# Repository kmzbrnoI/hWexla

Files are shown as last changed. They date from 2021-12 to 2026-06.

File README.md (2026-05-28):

hWexla – Switch motor
=====================

hWexla is a switch motor designed in [Model Railroader Club Brno I](https://kmz-brno.cz/)
to switch their turnouts. The project is opensource & openhardware, this repository
contains all data.

## Features

* Model 9g servo used as a drive force.
* Magnetic detection of movement. No mechanical parts detecting servo movement.
* Installation via unified D-SUB 25 connector.
* 2 inputs for position setting.
* 2 outputs for position indication (up to 200 mA).
* 2 IO pins for debug/panel.
* 2×3 relay for switching track current (up to 3 A).
* Diagnostic interface.
* IO protection.
* Slave mode.
* Input voltage: 10–20 V.
* Stabilizing of servo-voltage is solved in external board – hWexla contains
  only connector. Stepdowns like [RB0005](https://github.com/RoboticsBrno/RB0005-UniversalStepDown)
  are expected to be used.

## Parts

1. [PCB](pcb)
2. [Firmware](fw)
3. [WEXLACON PCB](wexlacon)
4. [Diagnostic PCB](diagpcb)

## [Requirements](requirements.md)

In czech only

## Piece check

Pass following checks to mark a piece of (newly manufactured) hWexla as
*quality check pass*.

1. Optical inspection.
2. Check programming interface is working.
3. Check diagnostic interface is working (browser visible, accepting commands).
4. Check all inputs are working (browser + functional test).
5. Check all outputs are working (browser + HW tester).
6. Check servo moves in full range.
7. Check magnet values, test signalization of end-position-reached.
8. Check relay output.
9. Monitor recorded minimum&maximum servo voltage.
10. Check for errors/warnings (browser).

## Authors

hWexla was designed in [Model Railroaders Club
Brno](https://www.kmz-brno.cz/) by [Jan Horáček](mailto:jan.horacek@kmz-brno.cz).

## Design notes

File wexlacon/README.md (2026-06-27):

WEXLACON
========

WEXLACON is a PCB permanently mounted to the railway layout to which hWexla connects.

Schematic and the PCB was designed in KiCad 9.

## Authors

hWexla was designed in [Model Railroaders Club
Brno](https://www.kmz-brno.cz/) by [Jan Horáček](mailto:jan.horacek@kmz-brno.cz).

## License

Content of this directory is provided under [Creative Commons
Attribution-ShareAlike 4.0
License](https://creativecommons.org/licenses/by-sa/4.0/) as openhardware
project. You may download any data, contribute to the project, manufacture PCB
yourself or even sell it yourself.

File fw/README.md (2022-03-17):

# hWexla firmware

## Build & requirements

This firmware is developed in C language, compiled via `avr-gcc` with help
of `make`. You may also find tools like `avrdude` helpful.

Hex files are available in *Releases* section.

## Programming

Firmware could be programmed directly to board via ISP programming connector.

Flash main application & fuses:

```bash
$ make
$ make fuses
$ make program
```

## Author's toolkit

Text editor + `make`. No more, no less.

## License

This application is released under the [Apache License v2.0
](https://www.apache.org/licenses/LICENSE-2.0).

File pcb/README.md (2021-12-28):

hWexla PCB
==========

See main repository readme for more information.

## License

Content of this directory is provided under [Creative Commons
Attribution-ShareAlike 4.0
License](https://creativecommons.org/licenses/by-sa/4.0/) as openhardware
project. You may download any data, contribute to the project, create PCB
yourself or even sell it yourself.

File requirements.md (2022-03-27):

Požadavky na přestavník hWexla
==============================

## Vstupy/výstupy

1. Přestavník má
 * 2 vstupy na nastavení polohy (z MTB),
 * 2 vstupy/výstupy do pultu/testovací krabičky,
 * 2 výstupy indikující polohu (do MTB).
2. Vstupy z MTB mají vždy přednost nad vstupy z přestavníku.
3. Všechny vstupy jsou chráněny proti přepětí.
4. Všechny výstupy jsou formou otevřeného kolektoru do maximálního externího
   napětí 30 V. Výstupy jsou chráněny proti přepětí.

## Hardware

1. Přestavník je chráněn proti přepětí. Připojení přepětí ho nepoškodí.
   Ochrana proti přepětí je samovratná.
2. Přestavník je chráněn proti opačné polaritě napájení. Připojení opačného
   napájení ho nepoškodí. Ochrana proti opačnému napájení je samovratná.
3. Přestavník je chráněn proti poruše serva. Při zkratu na servu dojde
   k přepálení nevratné pojistky.
4. Výstup stabilizovaných 5 V ven z desky je chráněn pojistkou.
5. Testovací a digitální vstupy a výstupy jsou chráněny proti krátkým napěťovým
   špičkám.
6. Stabilizace napájení pro servo je řešená pomocí externího modulu. Očekávaný
   je pulzní stepdown. Vyčlenění stabilizace z hlavní DPS umožňuje její snadné
   nahrazení například v případě nedostupných součástek.
7. Garantovaný proud přes relé je 3 A.

## Software

1. Relé se připíná uprostřed chodu přestavníku.
2. V případě nefunkčnosti serva (např. odpojení), je při manuálním dojetí
   do polohy správně ovládáno relé.
3. Koncová poloha je indikována na základě hodnot z magnetického senzoru.
   Hodnoty ze senzoru jinak nemají na funkci přestavníku žádný další vliv.
4. Přestavník kontroluje napájení serva.
5. Přestavník indikuje svůj stav pomocí LED.
6. Z přestavníku je možné číst diagnostická data pomocí USART rozhraní.
7. Pomocí testovací krabičky je možné nastavit obě koncové polohy.
8. Při startu přestavník zapne napájení serva až po pseudo-náhodné době, aby
   se rozložila proudová zátěž při zapínání kolejiště s mnoha přestavníky.

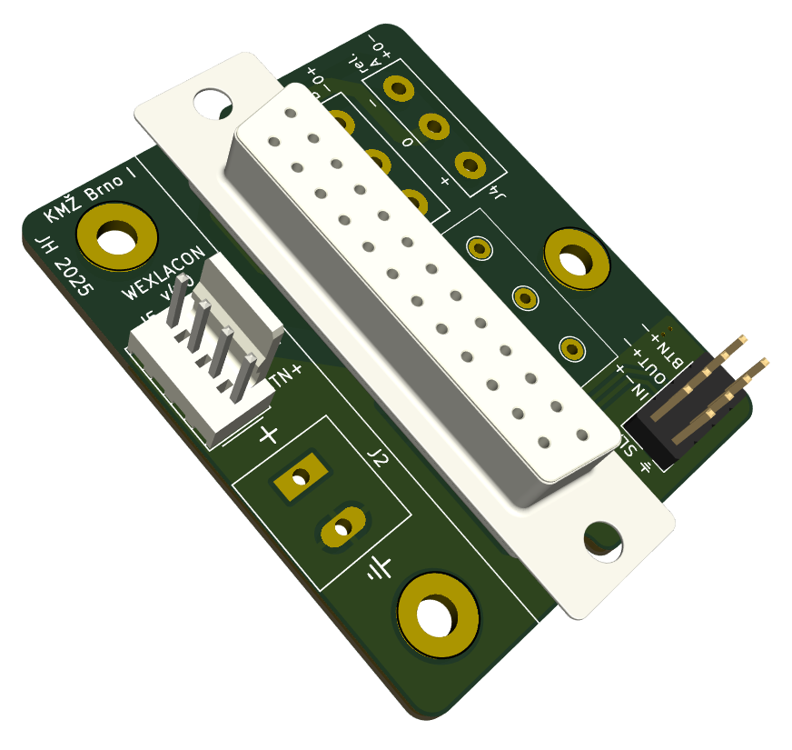
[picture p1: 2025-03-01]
wexlacon/export/wexlacon-3d.png

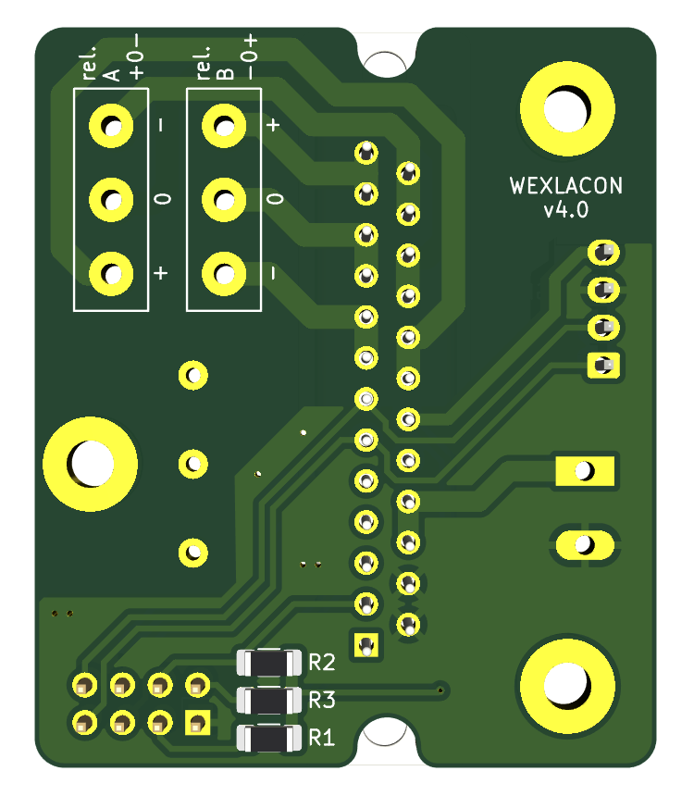
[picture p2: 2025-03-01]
wexlacon/export/wexlacon-bot.png

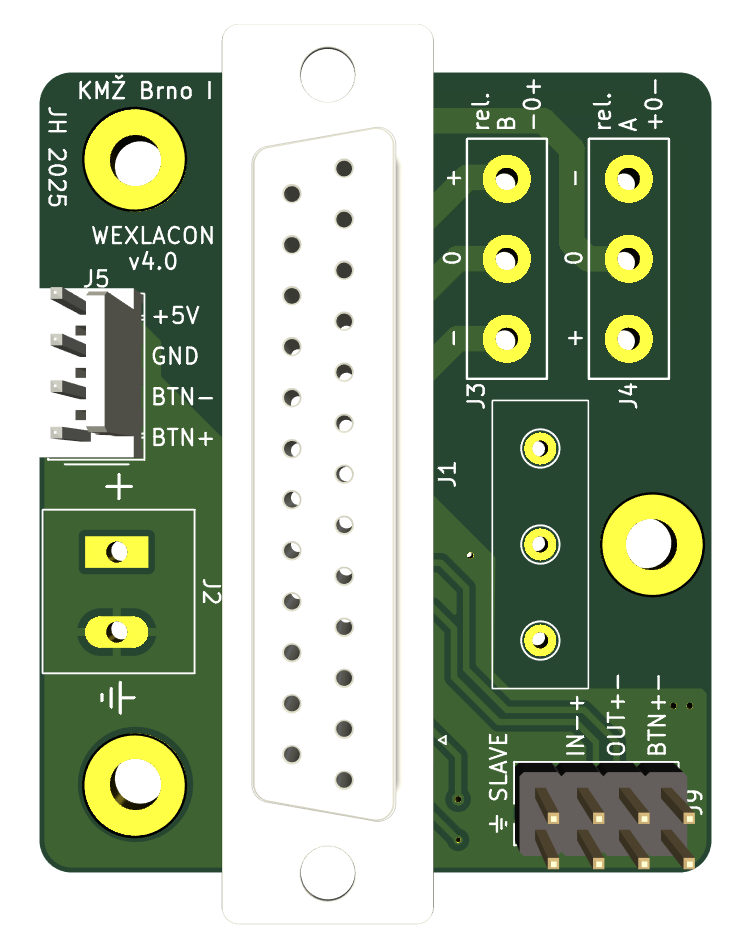
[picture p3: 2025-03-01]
wexlacon/export/wexlacon-top.png

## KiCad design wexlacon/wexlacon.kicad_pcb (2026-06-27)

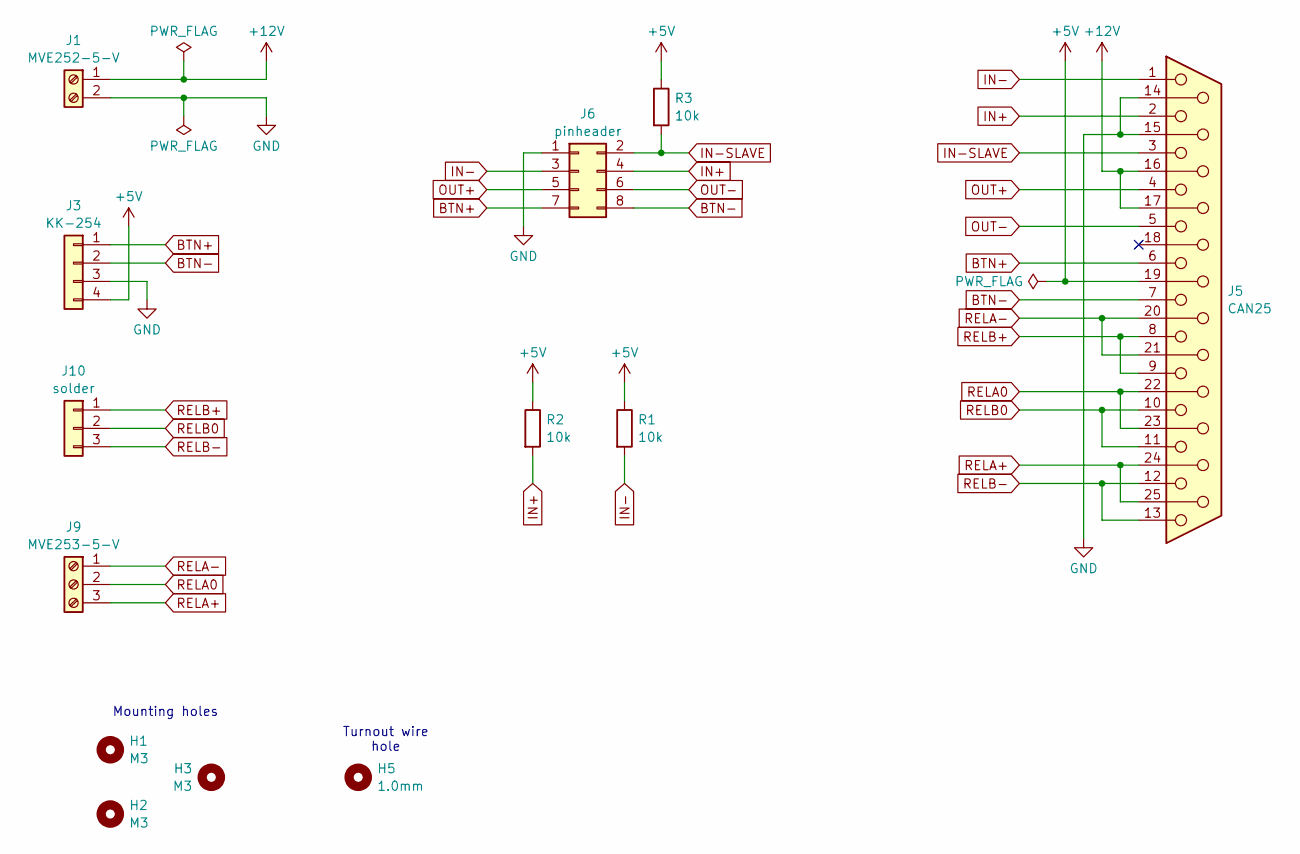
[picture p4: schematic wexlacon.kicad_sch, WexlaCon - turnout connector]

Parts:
H1, H2, H3: M3; MountingHole_3.2mm_M3_Pad
H5: 1.0mm; TestPoint_THTPad_D2.0mm_Drill1.0mm
J1: MVE252-5-V
J3: KK-254; Molex_KK-254_AE-6410-04A_1x04_P2.54mm_Vertical
J5: CAN25; DSUB-25_Female_Vertical_P2.77x2.84mm
J6: pinheader; PinHeader_2x04_P2.54mm_Vertical
J9: MVE253-5-V; RELAYCON
J10: solder; RELAYCON
R1, R2, R3: 10k; R_1206_3216Metric_Pad1.30x1.75mm_HandSolder

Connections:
+5V: J3.4, J5.19, R1.1, R2.1, R3.1
+12V: J1.1, J5.16, J5.17
BTN+: J3.1, J5.6, J6.7
BTN-: J3.2, J5.7, J6.8
GND: J1.2, J3.3, J5.14, J5.15, J6.1
IN+: J5.2, J6.4, R2.2
IN-: J5.1, J6.3, R1.2
IN-SLAVE: J5.3, J6.2, R3.2
OUT+: J5.4, J6.5
OUT-: J5.5, J6.6
RELA0: J5.22, J5.23, J9.2
RELA+: J5.24, J5.25, J9.3
RELA-: J5.20, J5.21, J9.1
RELB0: J5.10, J5.11, J10.2
RELB+: J5.8, J5.9, J10.1
RELB-: J5.12, J5.13, J10.3

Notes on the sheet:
Mounting holes
Turnout wire hole

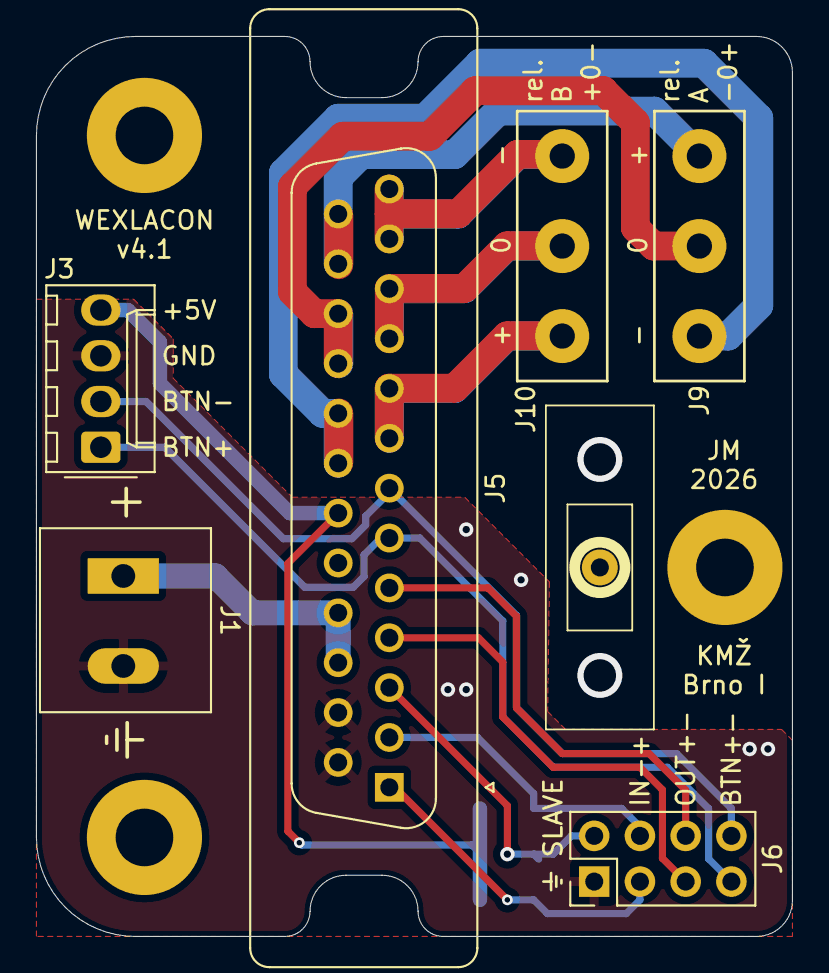
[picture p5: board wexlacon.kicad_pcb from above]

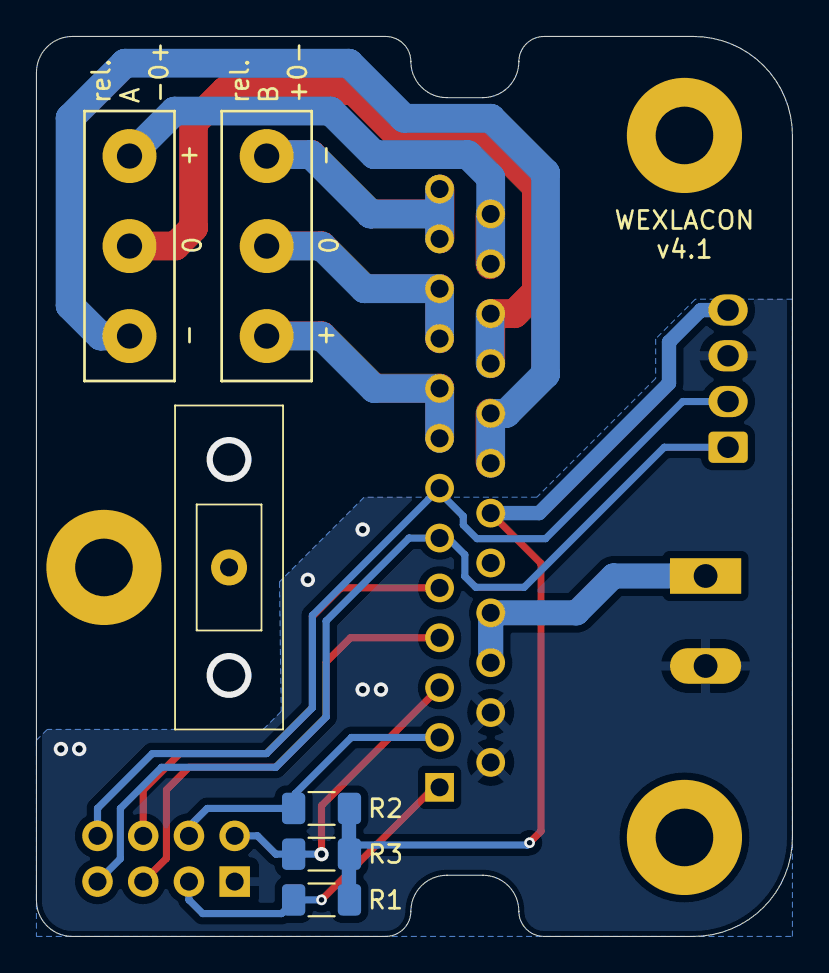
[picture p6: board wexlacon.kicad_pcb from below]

Board: 2 copper layers, 42.0 x 50.0 mm, 13 parts (3 on the bottom side), 16 nets.

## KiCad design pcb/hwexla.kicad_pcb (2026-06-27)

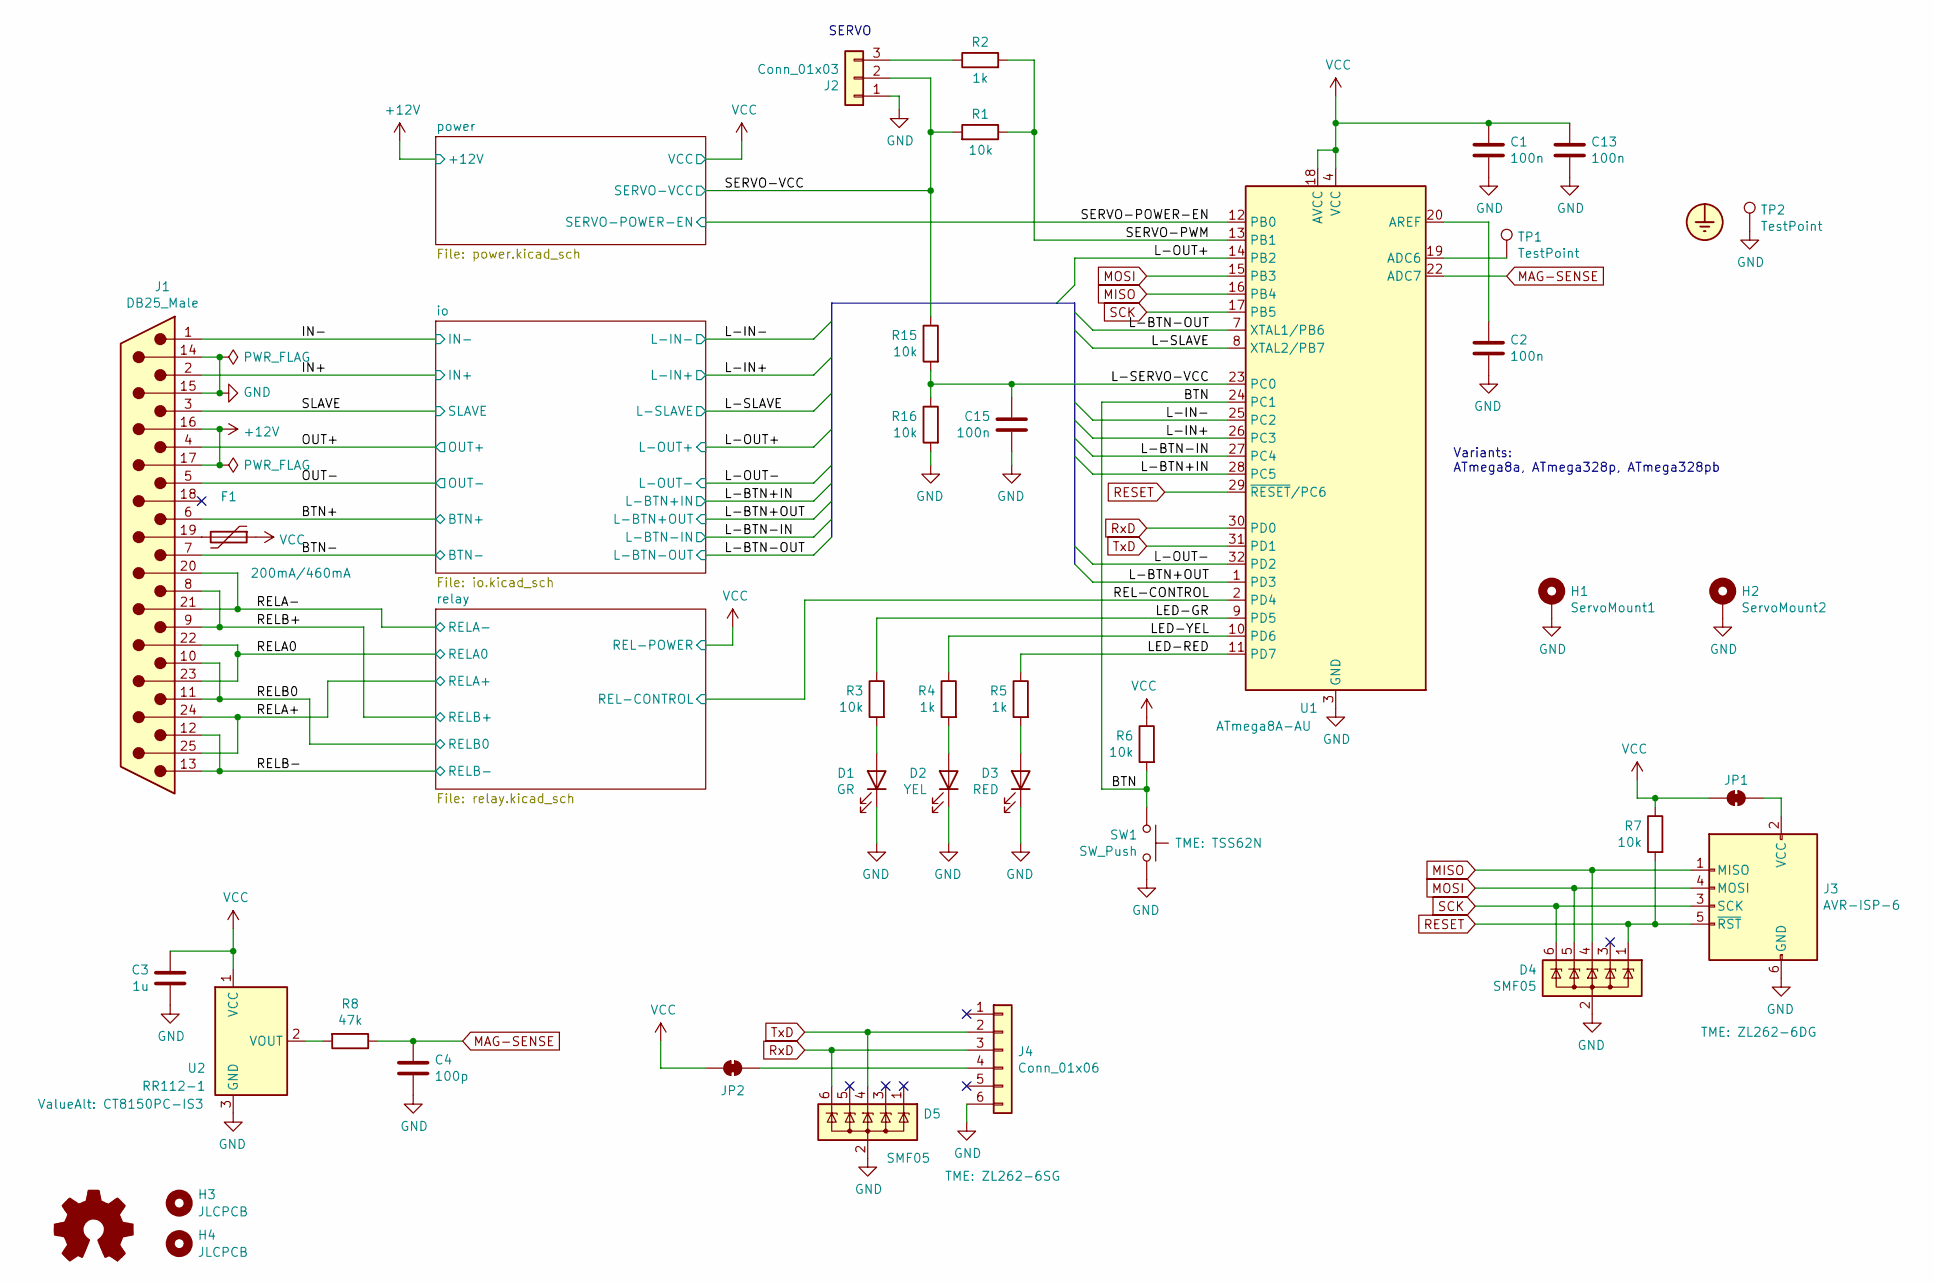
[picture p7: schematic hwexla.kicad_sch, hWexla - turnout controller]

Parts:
C1, C2, C13, C15: 100n; C_0805_2012Metric_Pad1.18x1.45mm_HandSolder; LCSC C49678
C3: 1u; C_0805_2012Metric_Pad1.18x1.45mm_HandSolder; LCSC C28323
C4: 100p; C_0805_2012Metric_Pad1.18x1.45mm_HandSolder; LCSC C1790
D1: GR; LED_0805_2012Metric_Pad1.15x1.40mm_HandSolder; LCSC C2297
D2: YEL; LED_0805_2012Metric_Pad1.15x1.40mm_HandSolder; LCSC C2296
D3: RED; LED_0805_2012Metric_Pad1.15x1.40mm_HandSolder; LCSC C84256
D4, D5: SMF05; SOT-363_SC-70-6; LCSC C15879
F1: 200mA/460mA; Fuse_1206_3216Metric_Pad1.42x1.75mm_HandSolder; LCSC C69680
H1: ServoMount1; MountingHole_2.2mm_M2_Pad
H2: ServoMount2; MountingHole_2.2mm_M2_Pad
H3, H4: JLCPCB; ToolingHole_1.152mm; JLCPCB_IGNORE true
J1: DB25_Male; DSUB-25_Male_EdgeMount_P2.77mm; JLCPCB_IGNORE true
J2: Conn_01x03; PinHeader_1x03_P2.54mm_Vertical; JLCPCB_IGNORE true
J3: AVR-ISP-6; PinSocket_2x03_P2.54mm_Vertical; JLCPCB_IGNORE true
J4: Conn_01x06; PinSocket_1x06_P2.54mm_Vertical; JLCPCB_IGNORE true
JP1, JP2: SolderJumper-2_P1.3mm_Bridged_RoundedPad1.0x1.5mm
R1, R3, R6, R7, R15, R16: 10k; R_0805_2012Metric_Pad1.20x1.40mm_HandSolder; LCSC C17414
R2, R4, R5: 1k; R_0805_2012Metric_Pad1.20x1.40mm_HandSolder; LCSC C17513
R8: 47k; R_0805_2012Metric_Pad1.20x1.40mm_HandSolder; LCSC C17713
SW1: SW_Push; SW_SPST_Omron_B3FS-100xP; JLCPCB_IGNORE true
TP1: TestPoint; TestPoint_Pad_D1.5mm
TP2: TestPoint; TestPoint_Loop_D1.80mm_Drill1.0mm_Beaded; JLCPCB_IGNORE true
U1: ATmega8A-AU; TQFP-32_7x7mm_P0.8mm; LCSC C16190
U2: RR112-1; SOT-23W; JLCPCB_IGNORE true

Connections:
+12V: J1.16, J1.17; also elsewhere on the board
/BTN: R6.2, SW1.2, U1.24 (PC1)
/BTN+: J1.6; also elsewhere on the board
/BTN-: J1.7; also elsewhere on the board
/IN+: J1.2; also elsewhere on the board
/IN-: J1.1; also elsewhere on the board
/L-BTN+IN: U1.28 (PC5); also elsewhere on the board
/L-BTN+OUT: U1.1 (PD3); also elsewhere on the board
/L-BTN-IN: U1.27 (PC4); also elsewhere on the board
/L-BTN-OUT: U1.7 (XTAL1/PB6); also elsewhere on the board
/L-IN+: U1.26 (PC3); also elsewhere on the board
/L-IN-: U1.25 (PC2); also elsewhere on the board
/L-OUT+: U1.14 (PB2); also elsewhere on the board
/L-OUT-: U1.32 (PD2); also elsewhere on the board
/L-SERVO-VCC: C15.1, R15.2, R16.1, U1.23 (PC0)
/L-SLAVE: U1.8 (XTAL2/PB7); also elsewhere on the board
/LED-GR: R3.1, U1.9 (PD5)
/LED-RED: R5.1, U1.11 (PD7)
/LED-YEL: R4.1, U1.10 (PD6)
/OUT+: J1.4; also elsewhere on the board
/OUT-: J1.5; also elsewhere on the board
/REL-CONTROL: U1.2 (PD4); also elsewhere on the board
/RELA0: J1.22, J1.23; also elsewhere on the board
/RELA+: J1.24, J1.25; also elsewhere on the board
/RELA-: J1.20, J1.21; also elsewhere on the board
/RELB0: J1.10, J1.11; also elsewhere on the board
/RELB+: J1.8, J1.9; also elsewhere on the board
/RELB-: J1.12, J1.13; also elsewhere on the board
/SERVO-POWER-EN: U1.12 (PB0); also elsewhere on the board
/SERVO-PWM: R1.1, R2.2, U1.13 (PB1)
/SERVO-VCC: J2.2, R1.2, R15.1; also elsewhere on the board
/SLAVE: J1.3; also elsewhere on the board
GND: C1.1, C2.1, C3.1, C4.2, C13.1, C15.2, D1.1 (K), D2.1 (K), D3.1 (K), D4.2 (A), D5.2 (A), H1.1, H2.1, J1.14, J1.15, J2.1, J3.6 (GND), J4.6, R16.2, SW1.1, TP2.1, U1.3 (GND), U1.5 (GND), U1.21 (GND), U2.3 (GND); also elsewhere on the board
MAG-SENSE: C4.1, R8.1, U1.22 (ADC7)
MISO: D4.4 (K), J3.1 (MISO), U1.16 (PB4)
MOSI: D4.5 (K), J3.4 (MOSI), U1.15 (PB3)
unnamed: D1.2 (A), R3.2
unnamed: D2.2 (A), R4.2
unnamed: D3.2 (A), R5.2
unnamed: F1.2, J1.19
unnamed: J2.3, R2.1
unnamed: J3.2 (VCC), JP1.1 (A)
unnamed: J4.4, JP2.2 (B)
unnamed: TP1.1, U1.19 (ADC6)
unnamed: C2.2, U1.20 (AREF)
unnamed: R8.2, U2.2 (VOUT)
RESET: D4.1 (K), J3.5 (~RST), R7.2, U1.29 (~RESET/PC6)
RxD: D5.6 (K), J4.3, U1.30 (PD0)
SCK: D4.6 (K), J3.3 (SCK), U1.17 (PB5)
TxD: D5.4 (K), J4.2, U1.31 (PD1)
VCC: C1.2, C3.2, C13.2, F1.1, JP1.2 (B), JP2.1 (A), R6.1, R7.1, U1.4 (VCC), U1.6 (VCC), U1.18 (AVCC), U2.1 (VCC); also elsewhere on the board

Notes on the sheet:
Variants: ATmega8a, ATmega328p, ATmega328pb
SERVO

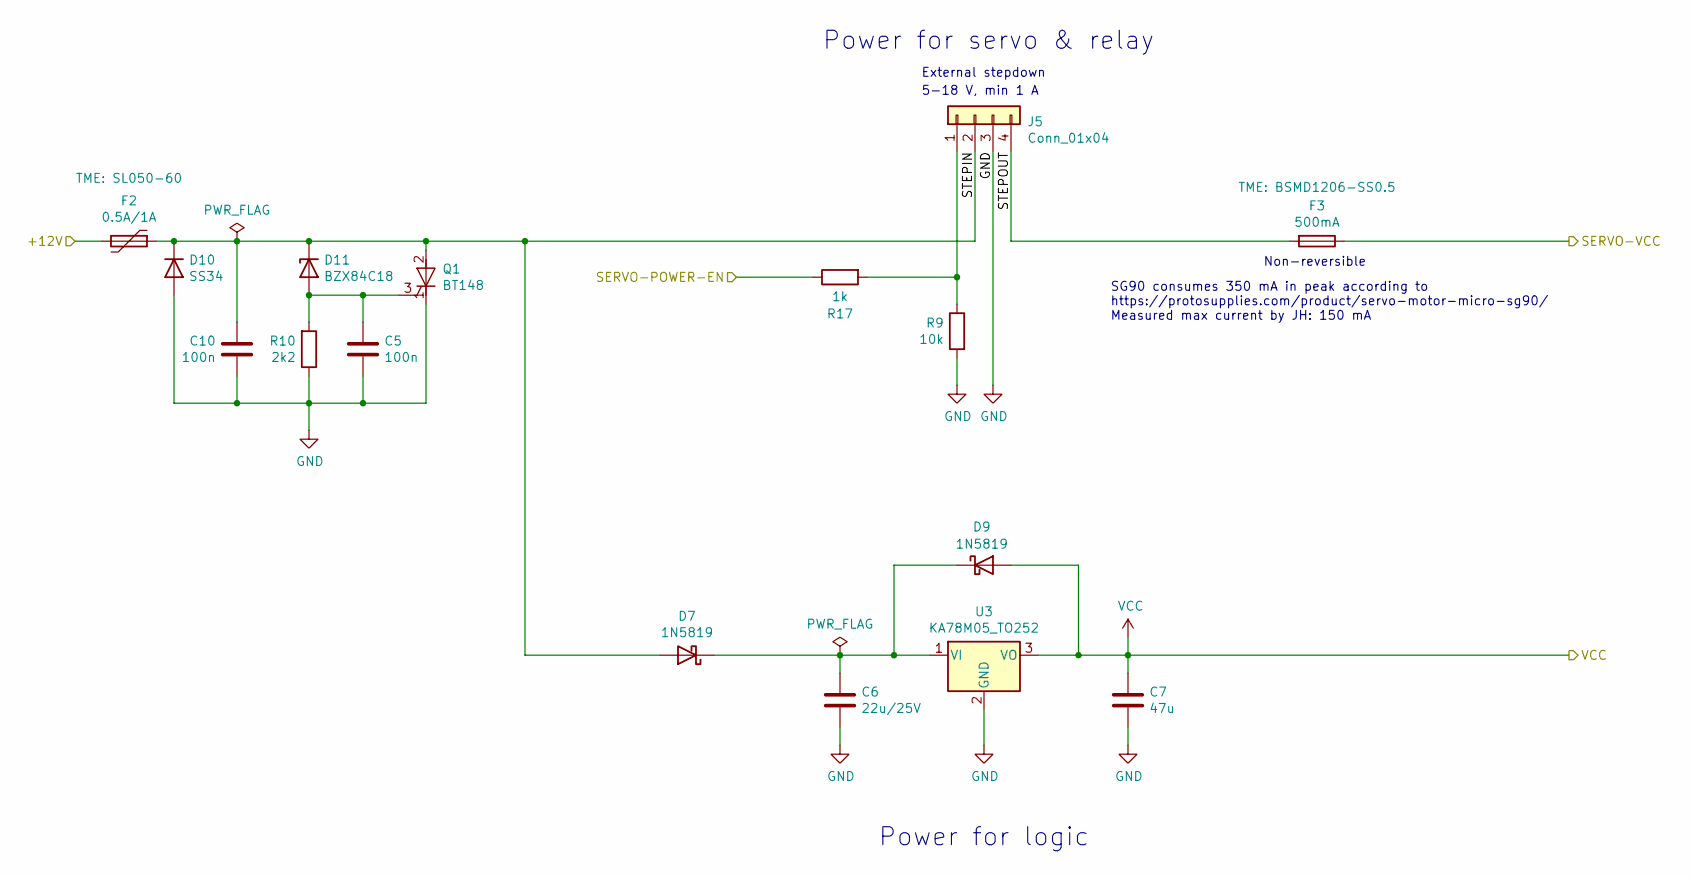
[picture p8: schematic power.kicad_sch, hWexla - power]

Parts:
C5, C10: 100n; C_0805_2012Metric_Pad1.18x1.45mm_HandSolder; LCSC C49678
C6: 22u/25V; C_0805_2012Metric; LCSC C45783
C7: 47u; C_0805_2012Metric; LCSC C16780
D7, D9: 1N5819; D_SOD-123; LCSC C191023
D10: SS34; D_SMA_Handsoldering; LCSC C8678
D11: BZX84C18; SOT-23; LCSC C841166
F2: 0.5A/1A; Fuse_2920_7451Metric; LCSC C2760297
F3: 500mA; Fuse_1206_3216Metric_Pad1.42x1.75mm_HandSolder; LCSC C3161978
J5: Conn_01x04; PinHeader_1x04_P2.54mm_Vertical; JLCPCB_IGNORE true
Q1: BT148; SOT-223; LCSC C256433
R9: 10k; R_0805_2012Metric_Pad1.20x1.40mm_HandSolder; LCSC C17414
R10: 2k2; R_0805_2012Metric_Pad1.20x1.40mm_HandSolder; LCSC C17520
R17: 1k; R_0805_2012Metric_Pad1.20x1.40mm_HandSolder; LCSC C17513
U3: KA78M05_TO252; TO-252-2; LCSC C58069

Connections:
+12V: F2.2; also elsewhere on the board
/SERVO-POWER-EN: R17.1; also elsewhere on the board
/SERVO-VCC: F3.1; also elsewhere on the board
/power/STEPIN: C10.1, D7.2 (A), D10.1 (K), D11.3 (K), F2.1, J5.2, Q1.2 (A)
/power/STEPOUT: F3.2, J5.4
GND: C5.2, C6.2, C7.2, C10.2, D10.2 (A), J5.3, Q1.1 (K), R9.2, R10.1, U3.2 (GND); also elsewhere on the board
unnamed: C6.1, D7.1 (K), D9.1 (K), U3.1 (VI)
unnamed: C5.1, D11.1 (A), Q1.3 (G), R10.2
unnamed: J5.1, R9.1, R17.2
VCC: C7.1, D9.2 (A), U3.3 (VO); also elsewhere on the board

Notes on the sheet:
Power for servo & relay
SG90 consumes 350 mA in peak according to https://protosupplies.com/product/servo-motor-micro-sg90/ Measured max current by JH: 150 mA
External stepdown
Non-reversible
Power for logic
5-18 V, min 1 A

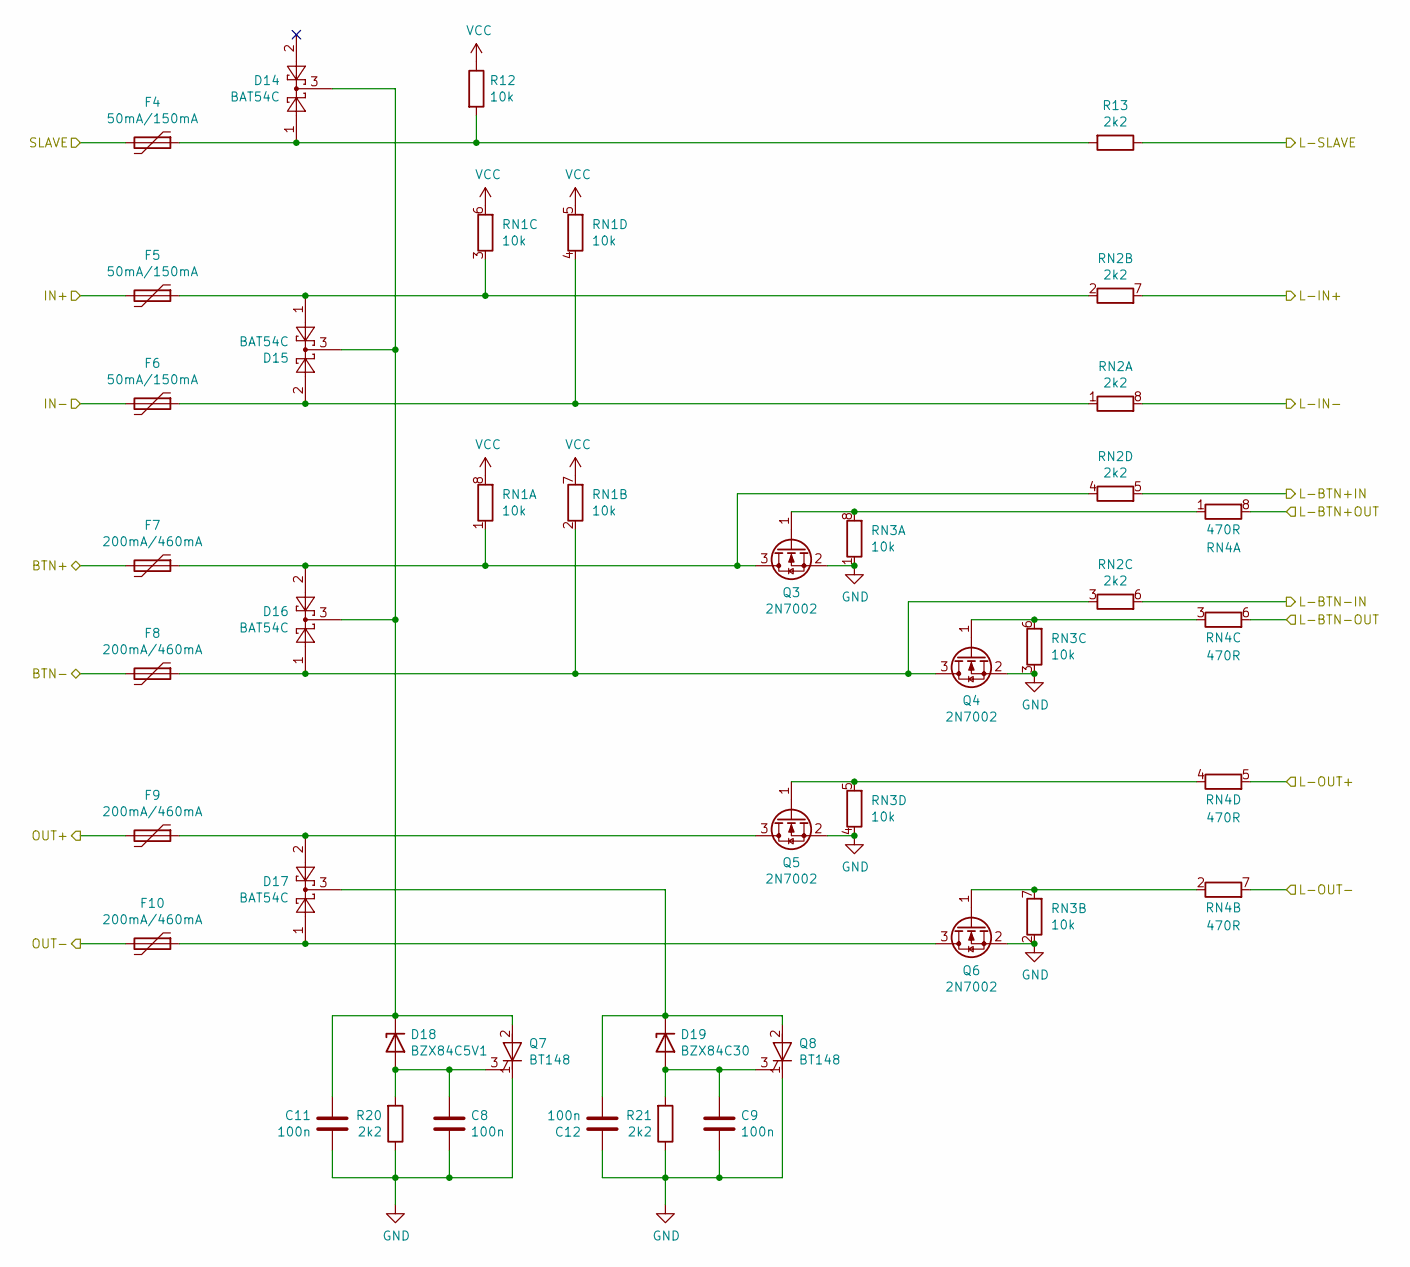
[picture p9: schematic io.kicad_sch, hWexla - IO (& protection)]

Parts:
C8, C9, C11, C12: 100n; C_0805_2012Metric_Pad1.18x1.45mm_HandSolder; LCSC C49678
D14, D15, D16, D17: BAT54C; SOT-23; LCSC C37704
D18: BZX84C5V1; SOT-23; LCSC C962733
D19: BZX84C30; SOT-23; LCSC C2926248
F4, F5, F6: 50mA/150mA; Fuse_1206_3216Metric_Pad1.42x1.75mm_HandSolder; LCSC C20797
F7, F8, F9, F10: 200mA/460mA; Fuse_1206_3216Metric_Pad1.42x1.75mm_HandSolder; LCSC C69680
Q3, Q4, Q5, Q6: 2N7002; SOT-23; LCSC C8545
Q7, Q8: BT148; SOT-223; LCSC C256433
R12: 10k; R_0805_2012Metric_Pad1.20x1.40mm_HandSolder; LCSC C17414
R13, R20, R21: 2k2; R_0805_2012Metric_Pad1.20x1.40mm_HandSolder; LCSC C17520
RN1, RN3: 10k; R_Array_Concave_4x0603; LCSC C396839
RN2: 2k2; R_Array_Concave_4x0603; LCSC C136829
RN4: 470R; R_Array_Concave_4x0603; LCSC C705088

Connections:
/BTN+: F7.2; also elsewhere on the board
/BTN-: F8.2; also elsewhere on the board
/IN+: F5.2; also elsewhere on the board
/IN-: F6.2; also elsewhere on the board
/L-BTN+IN: RN2.5 (R4.2); also elsewhere on the board
/L-BTN+OUT: RN4.8 (R1.2); also elsewhere on the board
/L-BTN-IN: RN2.6 (R3.2); also elsewhere on the board
/L-BTN-OUT: RN4.6 (R3.2); also elsewhere on the board
/L-IN+: RN2.7 (R2.2); also elsewhere on the board
/L-IN-: RN2.8 (R1.2); also elsewhere on the board
/L-OUT+: RN4.5 (R4.2); also elsewhere on the board
/L-OUT-: RN4.7 (R2.2); also elsewhere on the board
/L-SLAVE: R13.1; also elsewhere on the board
/OUT+: F9.2; also elsewhere on the board
/OUT-: F10.2; also elsewhere on the board
/SLAVE: F4.2; also elsewhere on the board
GND: C8.2, C9.2, C11.2, C12.1, Q3.2 (S), Q4.2 (S), Q5.2 (S), Q6.2 (S), Q7.1 (K), Q8.1 (K), R20.1, R21.1, RN3.1 (R1.1), RN3.2 (R2.1), RN3.3 (R3.1), RN3.4 (R4.1); also elsewhere on the board
unnamed: D14.1, F4.1, R12.2, R13.2
unnamed: C8.1, D18.1 (A), Q7.3 (G), R20.2
unnamed: C11.1, D14.3, D15.3, D16.3, D18.3 (K), Q7.2 (A)
unnamed: C9.1, D19.1 (A), Q8.3 (G), R21.2
unnamed: C12.2, D17.3, D19.3 (K), Q8.2 (A)
unnamed: D16.2, F7.1, Q3.3 (D), RN1.1 (R1.1), RN2.4 (R4.1)
unnamed: Q3.1 (G), RN3.8 (R1.2), RN4.1 (R1.1)
unnamed: D16.1, F8.1, Q4.3 (D), RN1.2 (R2.1), RN2.3 (R3.1)
unnamed: Q4.1 (G), RN3.6 (R3.2), RN4.3 (R3.1)
unnamed: D17.2, F9.1, Q5.3 (D)
unnamed: Q5.1 (G), RN3.5 (R4.2), RN4.4 (R4.1)
unnamed: D17.1, F10.1, Q6.3 (D)
unnamed: Q6.1 (G), RN3.7 (R2.2), RN4.2 (R2.1)
unnamed: D15.1, F5.1, RN1.3 (R3.1), RN2.2 (R2.1)
unnamed: D15.2, F6.1, RN1.4 (R4.1), RN2.1 (R1.1)
VCC: R12.1, RN1.5 (R4.2), RN1.6 (R3.2), RN1.7 (R2.2), RN1.8 (R1.2); also elsewhere on the board

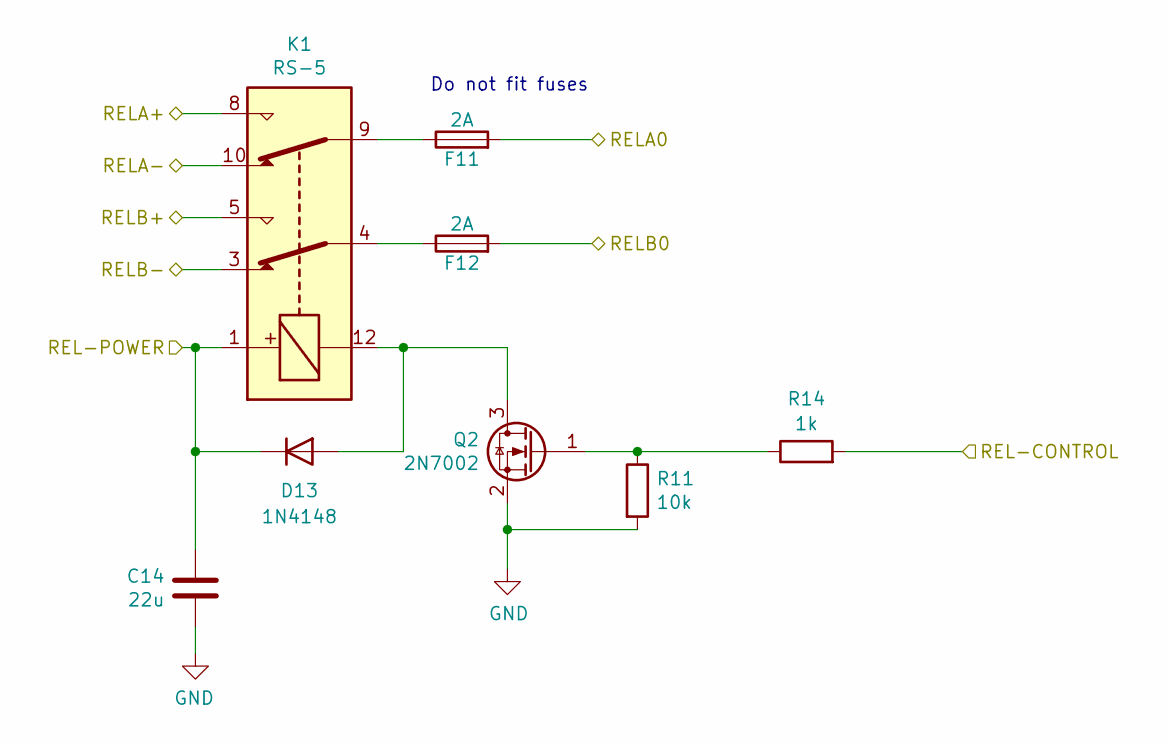
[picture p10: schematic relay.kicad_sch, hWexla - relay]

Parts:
C14: 22u; C_0805_2012Metric; LCSC C45783
D13: 1N4148; D_0805_2012Metric_Pad1.15x1.40mm_HandSolder; LCSC C2128
F11, F12: 2A; Fuse_1206_3216Metric_Pad1.42x1.75mm_HandSolder; LCSC C17888
K1: RS-5; HFD2; JLCPCB_IGNORE true
Q2: 2N7002; SOT-23; LCSC C8545
R11: 10k; R_0805_2012Metric_Pad1.20x1.40mm_HandSolder; LCSC C17414
R14: 1k; R_0805_2012Metric_Pad1.20x1.40mm_HandSolder; LCSC C17513

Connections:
/REL-CONTROL: R14.2; also elsewhere on the board
/RELA0: F11.2; also elsewhere on the board
/RELA+: K1.8; also elsewhere on the board
/RELA-: K1.10; also elsewhere on the board
/RELB0: F12.2; also elsewhere on the board
/RELB+: K1.5; also elsewhere on the board
/RELB-: K1.3; also elsewhere on the board
GND: C14.2, Q2.2 (S), R11.2; also elsewhere on the board
unnamed: D13.2 (A), K1.12, Q2.3 (D)
unnamed: F11.1, K1.9
unnamed: F12.1, K1.4
unnamed: Q2.1 (G), R11.1, R14.1
VCC: C14.1, D13.1 (K), K1.1; also elsewhere on the board

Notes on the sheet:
Do not fit fuses

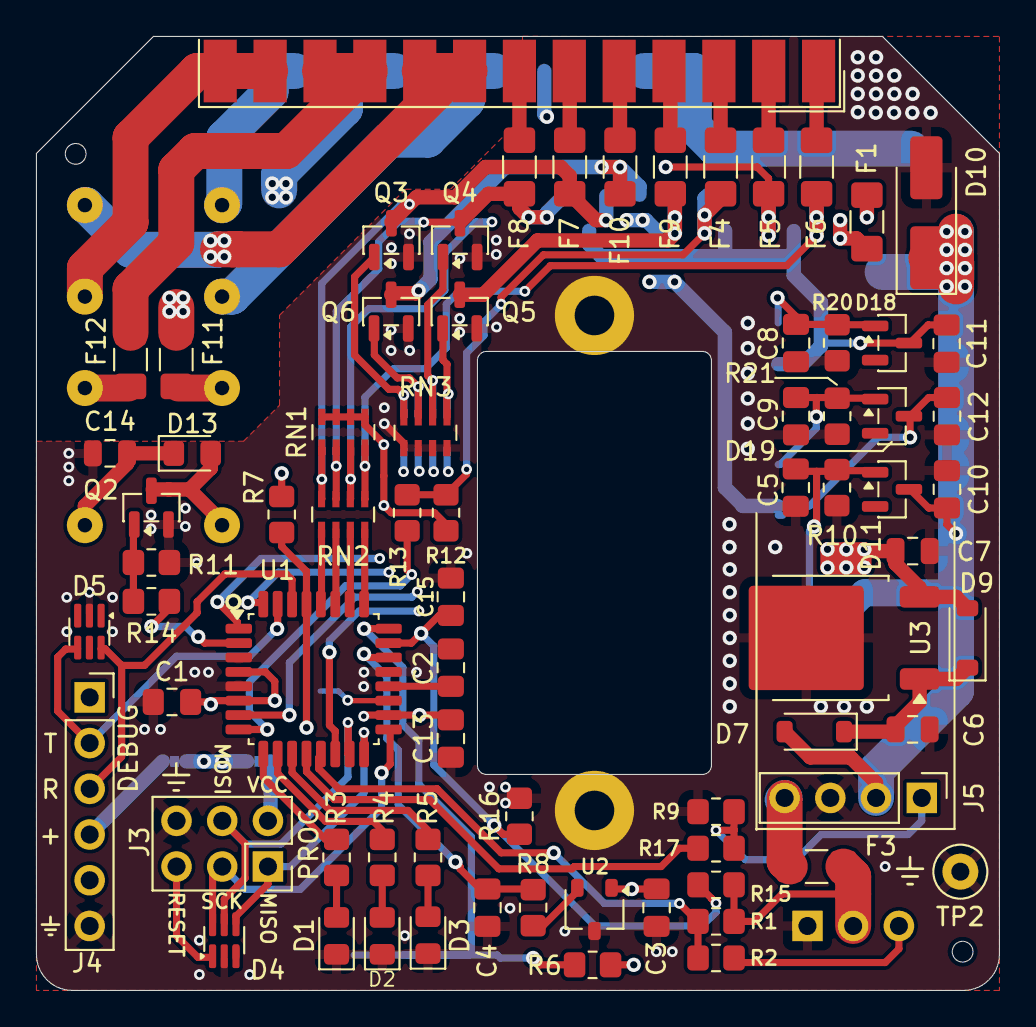
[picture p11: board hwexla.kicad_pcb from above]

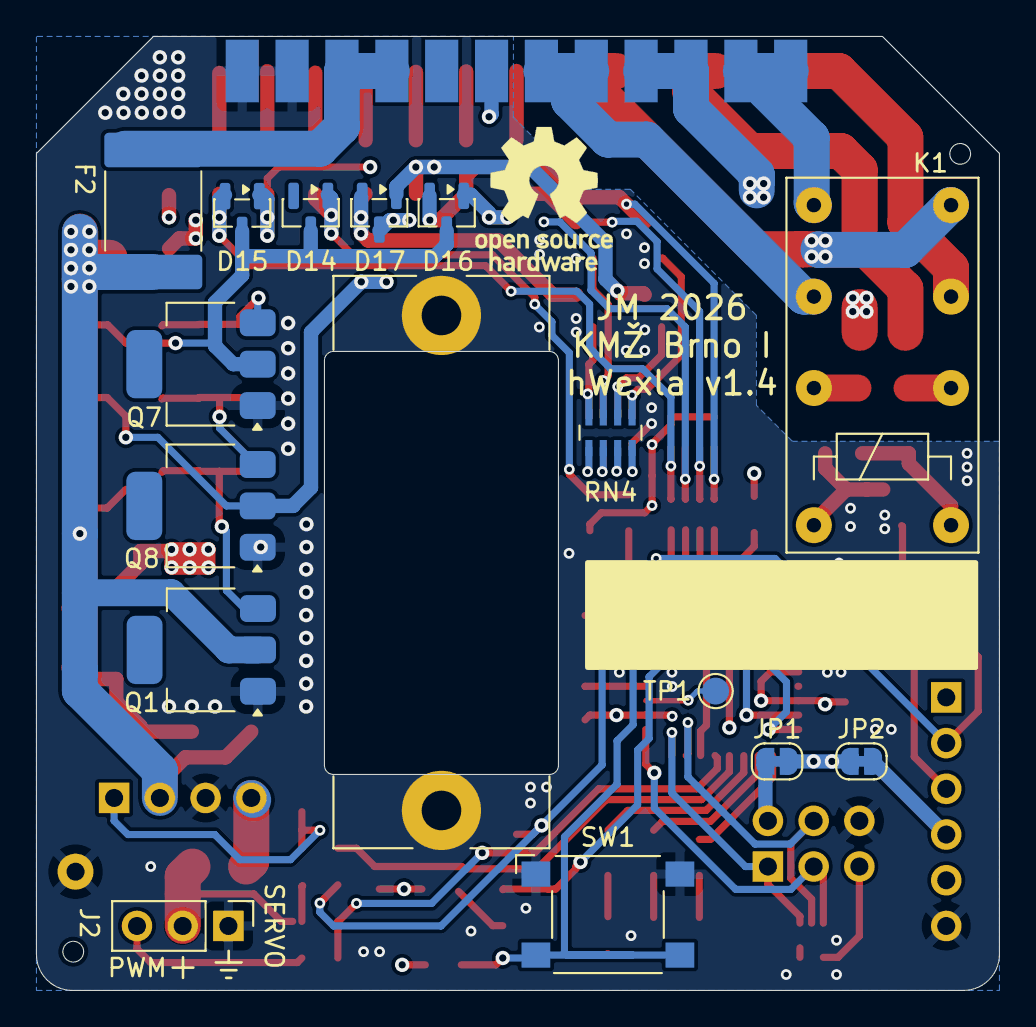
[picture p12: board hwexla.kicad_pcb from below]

Board: 4 copper layers, 53.5 x 53.0 mm, 92 parts (15 on the bottom side), 75 nets.

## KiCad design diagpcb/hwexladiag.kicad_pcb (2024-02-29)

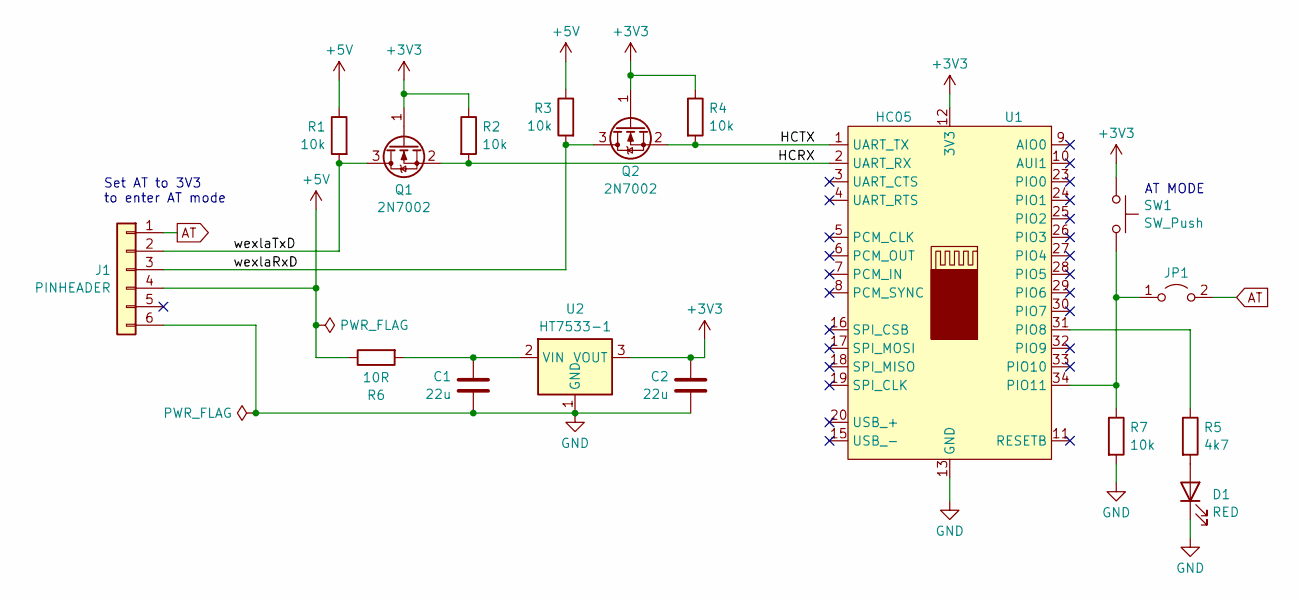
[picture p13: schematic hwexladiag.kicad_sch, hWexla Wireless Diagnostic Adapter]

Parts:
C1, C2: 22u; C_0805_2012Metric
D1: RED; LED_0805_2012Metric
J1: PINHEADER; PinHeader_1x06_P2.54mm_Vertical_SMD_Pin1Left
JP1: SolderJumper-2_P1.3mm_Open_RoundedPad1.0x1.5mm
Q1, Q2: 2N7002; SOT-23
R1, R2, R3, R4, R7: 10k; R_0805_2012Metric
R5: 4k7; R_0805_2012Metric
R6: 10R; R_0805_2012Metric
SW1: SW_Push; SW_SPST_EVQPE1
U1: HC05
U2: HT7533-1; SOT-89-3

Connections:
+3V3: C2.1, Q1.1 (G), Q2.1 (G), R2.1, R4.1, SW1.1, U1.12 (3V3), U2.3 (VOUT)
+5V: J1.4, R1.1, R3.1, R6.1
/HCRX: Q1.2 (S), R2.2, U1.2 (UART_RX)
/HCTX: Q2.2 (S), R4.2, U1.1 (UART_TX)
/wexlaRxD: J1.3, Q2.3 (D), R3.2
/wexlaTxD: J1.2, Q1.3 (D), R1.2
AT: J1.1, JP1.2 (B)
GND: C1.2, C2.2, D1.1 (K), J1.6, R7.2, U1.13 (GND), U1.21 (GND), U1.22 (GND), U2.1 (GND)
unnamed: D1.2 (A), R5.2
unnamed: JP1.1 (A), R7.1, SW1.2, U1.34 (PIO11)
unnamed: R5.1, U1.31 (PIO8)
unnamed: C1.1, R6.2, U2.2 (VIN)

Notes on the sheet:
Set AT to 3V3 to enter AT mode
AT MODE

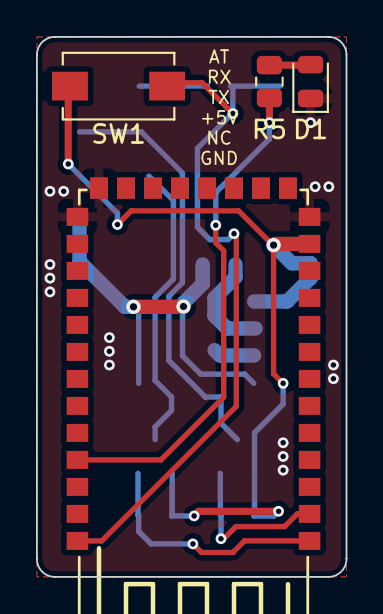
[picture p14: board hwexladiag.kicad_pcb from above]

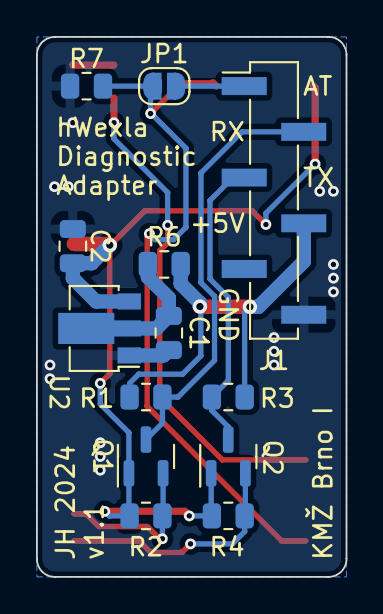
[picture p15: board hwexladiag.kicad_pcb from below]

Board: 2 copper layers, 17.2 x 30.0 mm, 17 parts (13 on the bottom side), 12 nets.

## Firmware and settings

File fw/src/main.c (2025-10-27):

/* Main source file of hWexla ATmega CPU.
 */

#include <stdint.h>
#include <stdbool.h>
#include <util/delay.h>
#include <avr/interrupt.h>
#include <avr/io.h>
#include <avr/wdt.h>
#include <avr/eeprom.h>
#include <avr/boot.h>
#include <util/atomic.h>
#include <stdlib.h>

#include "io.h"
#include "pwm_servo_gen.h"
#include "switch.h"
#include "inputs.h"
#include "eeprom.h"
#include "usart.h"
#include "diag.h"

///////////////////////////////////////////////////////////////////////////////

int main();
static void init(void);
static void set_outputs(void);
static void programming_enter(void);
static void programming_leave(void);
static void init_done(void);
static void leds_update(void);
static void inputs_poll(void);
bool magnet_isclose(uint16_t value, uint8_t threshold);

///////////////////////////////////////////////////////////////////////////////

#define BTN_FLICK_PERIOD 150 // ms (max uint8_t)
#define LED_FLICK_PERIOD 500 // ms (max uint16_t)
#define LED_FLICK_ON 250 // ms
#define PROG_BTN_MAX 20 // ms
#define INIT_ADC_VCC_LIMIT 5 // cca 250 ms
#define DIAG_UPDATE_PERIOD 200 // 200 ms
#define WARN_IND_MAX 10000 // 10 s
#define WARN_IND_BEGIN 9000

FailCode fail_code = fNoFail;
Warnings warnings;

volatile Turnout turnout;
volatile Mode mode;

volatile bool btn_flick = false;
volatile uint8_t prog_btn_counter_ms = 0;
volatile uint8_t pseudorand = 0;
uint8_t init_adc_vcc_ok_count = 0;
uint8_t init_adc_vcc_nok_count = 0;
volatile uint8_t diag_counter = 0;
volatile bool isr_switch_update_req = false;
volatile uint16_t led_flick_counter = 0; // note: read in ATOMIC_BLOCK!
volatile uint16_t warn_ind_counter = 0; // warning indication on outputs; note: read in ATOMIC_BLOCK!

///////////////////////////////////////////////////////////////////////////////

int main() {
	init();

	while (true) {
		inputs_update();
		inputs_poll();
		adc_poll();
		warnings.sep.magnet = magnet_iswarn();
		diag_read();
		leds_update();
		set_outputs();

		if (isr_switch_update_req) {
			switch_update();
			isr_switch_update_req = false;
		}

		// Saving to EEPROM can take a really long time -> save only if eeprom is ready
		if (ee_to_save) {
			if (ee_save()) {
				ee_to_save = false;
				ee_to_save_servo_vcc = false;
			}
		}
		else if (ee_to_save_servo_vcc) {
			if (ee_save_servo_vcc())
				ee_to_save_servo_vcc = false;
		}
		else if (ee_to_save_pos_plus) {
			if (ee_save_pos_plus())
				ee_to_save_pos_plus = false;
		}
		else if (ee_to_save_pos_minus) {
			if (ee_save_pos_minus())
				ee_to_save_pos_minus = false;
		}

		if (diag_counter >= DIAG_UPDATE_PERIOD) {
			diag_send();
			diag_counter = 0;
		}

		wdt_reset();
	}
}

void init(void) {
	ACSR |= ACD;  // analog comparator disable
	TIMSK = 0;
	mode = mInitializing;
	warnings.all = 0;

	io_init();
	set_output(PIN_LED_RED, true);
	set_output(PIN_LED_YELLOW, true);

	inputs_init();
	ee_load();
	pwm_servo_init();
	usart_initialize();

	bool reset_wanted = eeprom_read_byte(EEPROM_ADDR_RESET_WANTED);
	if ((((MCUCSR >> WDRF) & 1)) && (!reset_wanted)) {
		warnings.sep.wdg_reset = true;
		ee_to_save = true;
	}
	eeprom_update_byte(EEPROM_ADDR_RESET_WANTED, 0);

	// Timer 2 @ 1 kHz (1 ms)
	TCCR2 = (1 << WGM21) | (1 << CS21) | (1 << CS20); // CTC; prescaler 32×
	OCR2 = 248; // 1 ms
	TIMSK |= (1 << OCIE2);

	// Delay turning-on servo power for pseudorandom time
	uint8_t delay = (turnout.moved_plus % 10)+2; // 100-600 ms; step=50 ms
	for (size_t i = 0; i < delay; i++)
		_delay_ms(50);

	set_output(PIN_SERVO_POWER_EN, true);
	pwm_servo_gen(turnout.angle);

	if (mode == mFail) // failed during startup
		fail(fail_code); // fail again to reset outputs

	sei(); // enable interrupts globally
	wdt_enable(WDTO_60MS);
}

ISR(BADISR_vect) {
	fail(fBadISR);
}

///////////////////////////////////////////////////////////////////////////////

ISR(TIMER2_COMP_vect) {
	// Timer 2 @ 1 kHz (1 ms)
	// Execution on this timer taked ~100 us
	inputs_update_1ms();

	static uint8_t counter_20ms = 0;
	counter_20ms++;
	if (counter_20ms >= 20) {
		counter_20ms = 0;
		if ((isr_switch_update_req) && (mode != mFail))
			warnings.sep.missed_timer = true;
		isr_switch_update_req = true;
	}

	static uint8_t counter_50ms = 0;
	counter_50ms++;
	if (counter_50ms >= 50) {
		adc_start_measure();
		counter_50ms = 0;
	}

	static uint8_t flick_counter = 0;
	flick_counter++;
	if (flick_counter >= BTN_FLICK_PERIOD) {
		btn_flick = !btn_flick;
		flick_counter = 0;
	}

	if (prog_btn_counter_ms < 0xFF)
		prog_btn_counter_ms++;

	if (diag_counter < DIAG_UPDATE_PERIOD)
		diag_counter++;

	led_flick_counter++;
	if (led_flick_counter >= LED_FLICK_PERIOD)
		led_flick_counter = 0;

	warn_ind_counter++;
	if (warn_ind_counter > WARN_IND_MAX)
		warn_ind_counter = 0;

	pseudorand++;
}

///////////////////////////////////////////////////////////////////////////////

void on_switch_done(void) {
	if (turnout.position == tpPlus)
		ee_to_save_pos_plus = true;
	else
		ee_to_save_pos_minus = true;
}

void on_btn_pressed(uint8_t button) {
	switch (button) {
	case DEB_BTN:
		if (mode == mRun)
			programming_enter();
		else if (mode == mProgramming)
			programming_leave();
		else if (mode == mOverride)
			override_leave();
		else if (mode == mFail)
			reset();
		break;
	}
}

///////////////////////////////////////////////////////////////////////////////

void inputs_poll(void) {
	if (mode == mRun) {
		if ((in_debounced[DEB_IN_PLUS]) && (!in_debounced[DEB_IN_MINUS]))
			switch_turnout(tpPlus);
		if ((in_debounced[DEB_IN_MINUS]) && (!in_debounced[DEB_IN_PLUS]))
			switch_turnout(tpMinus);

		if ((!in_debounced[DEB_IN_PLUS]) && (!in_debounced[DEB_IN_MINUS])) {
			if ((in_debounced[DEB_BTN_PLUS]) && (!in_debounced[DEB_BTN_MINUS]))
				switch_turnout(tpPlus);
			if ((in_debounced[DEB_BTN_MINUS]) && (!in_debounced[DEB_BTN_PLUS]))
				switch_turnout(tpMinus);
		}

	} else if (mode == mProgramming) {
		if (prog_btn_counter_ms < PROG_BTN_MAX)
			return;

		if ((in_debounced[DEB_BTN_PLUS]) && (!in_debounced[DEB_BTN_MINUS])) {
			if (turnout.angle < PWM_ANGLE_MAX) {
				prog_btn_counter_ms = 0;
				turnout.angle += 1;
				pwm_servo_gen(turnout.angle);
			}
		}
		if ((in_debounced[DEB_BTN_MINUS]) && (!in_debounced[DEB_BTN_PLUS])) {
			if (turnout.angle > PWM_ANGLE_MIN) {
				prog_btn_counter_ms = 0;
				turnout.angle -= 1;
				pwm_servo_gen(turnout.angle);
			}
		}

	}
}

bool magnet_isclose(uint16_t value, uint8_t threshold) {
	return abs((int16_t)mag_value-(int16_t)value) < threshold;
}

bool magnet_iswarn(void) {
	// Hysteresis calculation
	static bool magnet_plus = false;
	static bool magnet_minus = false;
	magnet_plus = hysteresis(magnet_plus, !magnet_isclose(turnout.sensor_plus, MAG_THRESHOLD_WARN_OUT),
		magnet_isclose(turnout.sensor_plus, MAG_THRESHOLD_WARN_IN));
	magnet_minus = hysteresis(magnet_minus, !magnet_isclose(turnout.sensor_minus, MAG_THRESHOLD_WARN_OUT),
		magnet_isclose(turnout.sensor_minus, MAG_THRESHOLD_WARN_IN));

	if (turnout.position == tpPlus)
		return !magnet_plus;
	else if (turnout.position == tpMinus)
		return !magnet_minus;

	return false;
}

void set_outputs(void) {
	// Hysteresis calculation
	static bool magnet_plus = false;
	static bool magnet_minus = false;
	magnet_plus = hysteresis(magnet_plus, !magnet_isclose(turnout.sensor_plus, MAG_THRESHOLD_OK_OUT),
		magnet_isclose(turnout.sensor_plus, MAG_THRESHOLD_OK_IN));
	magnet_minus = hysteresis(magnet_minus, !magnet_isclose(turnout.sensor_minus, MAG_THRESHOLD_OK_OUT),
		magnet_isclose(turnout.sensor_minus, MAG_THRESHOLD_OK_IN));

	bool my_plus = (turnout.position == tpPlus) && (magnet_plus);
	bool my_minus = (turnout.position == tpMinus) && (magnet_minus);

	bool warn_output_active = ((my_plus) || (my_minus)) && (warnings.all > 0) \
		&& (!in_debounced[DEB_IN_PLUS]) && (!in_debounced[DEB_IN_MINUS]);
	if (warn_output_active) {
		ATOMIC_BLOCK(ATOMIC_FORCEON) {
			warn_output_active &= (warn_ind_counter >= WARN_IND_BEGIN);
		}
	}

	if ((mode == mRun) || (mode == mOverride)) {
		bool slave_both = (in_debounced[DEB_SLAVE] && in_debounced[DEB_IN_PLUS] && in_debounced[DEB_IN_MINUS]); // indicate slave's fail
		set_output(PIN_OUT_PLUS, ((my_plus || warn_output_active) && (!in_debounced[DEB_SLAVE] || in_debounced[DEB_IN_PLUS])) || slave_both);
		set_output(PIN_OUT_MINUS, ((my_minus || warn_output_active) && (!in_debounced[DEB_SLAVE] || in_debounced[DEB_IN_MINUS])) || slave_both);
		set_output(PIN_BTN_PLUS_OUT, my_plus || (turnout.position == tpMovingToPlus && btn_flick));
		set_output(PIN_BTN_MINUS_OUT, my_minus || (turnout.position == tpMovingToMinus && btn_flick));
	} else {
		set_output(PIN_OUT_PLUS, false);
		set_output(PIN_OUT_MINUS, false);
		set_output(PIN_BTN_PLUS_OUT, mode == mFail); // needs to be false to read both buttons
		set_output(PIN_BTN_MINUS_OUT, mode == mFail); // needs to be false to read both buttons
	}

	// Do not use sensor value to allow relay switching without physical servo
	if (mode == mFail) {
		set_output(PIN_RELAY_CONTROL, false);
	} else {
		if (turnout.position == tpPlus)
			set_output(PIN_RELAY_CONTROL, RELAY_STATE_PLUS);
		else if (turnout.position == tpMinus)
			set_output(PIN_RELAY_CONTROL, !RELAY_STATE_PLUS);
	}
}

///////////////////////////////////////////////////////////////////////////////

void programming_enter(void) {
	if ((turnout.position != tpPlus) && (turnout.position != tpMinus))
		return; // allow programming entry only when not moving

	mode = mProgramming;
	pwm_servo_gen(turnout.angle);
}

void programming_leave(void) {
	mode = mRun;
	pwm_servo_stop();

	if (turnout.position == tpPlus) {
		turnout.angle_plus = turnout.angle;
		turnout.sensor_plus = mag_value;
	} else if (turnout.position == tpMinus) {
		turnout.angle_minus = turnout.angle;
		turnout.sensor_minus = mag_value;
	}

	ee_to_save = true;
}

void override_enter(void) {
	mode = mOverride;
	ee_to_save = true;
}

void override_leave(void) {
	mode = mRun;
	ee_to_save = true;
}

void init_done(void) {
	pwm_servo_stop();
	mode = (ee_mode() == 1) ? mOverride : mRun;
}

void fail(FailCode code) {
	set_output(PIN_LED_GREEN, false);
	set_output(PIN_LED_YELLOW, false);
	set_output(PIN_SERVO_POWER_EN, false);

	// Set IO as inputs to allow external voltage to be applied (protection & hardware fixing)
	pin_mode(PIN_SERVO_POWER_EN, INPUT);
	pin_mode(PIN_SERVO_PWM, INPUT);
	pin_mode(PIN_RELAY_CONTROL, INPUT);

	fail_code = code;
	mode = mFail;
	ee_fail(code);
}

void reset(void) {
	eeprom_update_byte(EEPROM_ADDR_RESET_WANTED, true);
	cli();
	while (true);
}

///////////////////////////////////////////////////////////////////////////////

void leds_update(void) {
	bool flick_on;
	ATOMIC_BLOCK(ATOMIC_FORCEON) {
		flick_on = (led_flick_counter < LED_FLICK_ON);
	}
	set_output(PIN_LED_GREEN, (mode == mRun) || (mode == mInitializing) ||
		(((mode == mProgramming) || (mode == mOverride)) && (flick_on)));
	set_output(PIN_LED_YELLOW, (flick_on) &&
		(((mode == mRun) && (warnings.all > 0)) || (mode == mOverride)));
	set_output(PIN_LED_RED, (mode == mFail) && (flick_on));
}

///////////////////////////////////////////////////////////////////////////////

void on_adc_done(void) {
	if (mode == mInitializing) {
		if ((servo_vcc_value >= SERVO_VCC_MIN) && (servo_vcc_value <= SERVO_VCC_MAX)) {
			init_adc_vcc_ok_count++;
			if (init_adc_vcc_ok_count >= INIT_ADC_VCC_LIMIT)
				init_done();
		} else {
			init_adc_vcc_ok_count = 0;
			init_adc_vcc_nok_count++;
			if (init_adc_vcc_nok_count >= INIT_ADC_VCC_LIMIT)
				fail(fInitServoVCC);
		}

	} else if (mode != mFail) {
		if ((servo_vcc_value < SERVO_VCC_MIN) || (servo_vcc_value > SERVO_VCC_MAX))
			fail(fServoVCC);

		if (servo_vcc_value < servo_vcc_recorded_min) {
			servo_vcc_recorded_min = servo_vcc_value;
			ee_to_save_servo_vcc = true;
		}
		if (servo_vcc_value > servo_vcc_recorded_max) {
			servo_vcc_recorded_max = servo_vcc_value;
			ee_to_save_servo_vcc = true;
		}

		if ((servo_vcc_value < SERVO_VCC_MIN_WARN) && (!warnings.sep.servo_vcc_low)) {
			warnings.sep.servo_vcc_low = true;
			ee_to_save = true;
		}
		if ((servo_vcc_value > SERVO_VCC_MAX_WARN) && (!warnings.sep.servo_vcc_high)) {
			warnings.sep.servo_vcc_high = true;
			ee_to_save = true;
		}
	}
}

///////////////////////////////////////////////////////////////////////////////

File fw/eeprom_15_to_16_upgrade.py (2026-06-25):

#!/usr/bin/env python3

import sys
import subprocess

EEPROM_ADDR_POS_PLUS = 0x20
EEPROM_ADDR_POS_MINUS = 0x22
EEPROM_POS_BYTES = 2

def main() -> None:
    if len(sys.argv) < 2:
        sys.stderr.write(f'Usage: {sys.argv[0]} hwexla-programmer-device\n')
        sys.exit(1)

    device = sys.argv[1]
    avrdude_header = [
        'avrdude',
        '-p', 'atmega8',
        '-P', device,
        '-c', 'stk500',
    ]

    print('Erasing device flash...')
    subprocess.run(avrdude_header + ['-e'])

    print('Reading EEPROM...')
    subprocess.run(avrdude_header + ['-U', 'eeprom:r:eeprom_read.bin'])

    with open('eeprom_read.bin', 'rb') as eeprom_file:
        eeprom_content = bytearray(eeprom_file.read())

    pos_plus = (eeprom_content[EEPROM_ADDR_POS_PLUS]) | (eeprom_content[EEPROM_ADDR_POS_PLUS+1] << 8)
    pos_minus = (eeprom_content[EEPROM_ADDR_POS_MINUS]) | (eeprom_content[EEPROM_ADDR_POS_MINUS+1] << 8)
    print(f'old_pos_plus={pos_plus}')
    print(f'old_pos_minus={pos_minus}')
    pos_plus += 250
    pos_minus += 250
    print(f'new_pos_plus={pos_plus}')
    print(f'ne_pos_minus={pos_minus}')

    eeprom_content[EEPROM_ADDR_POS_PLUS] = (pos_plus & 0xFF)
    eeprom_content[EEPROM_ADDR_POS_PLUS+1] = ((pos_plus>>8) & 0xFF)
    eeprom_content[EEPROM_ADDR_POS_MINUS] = (pos_minus & 0xFF)
    eeprom_content[EEPROM_ADDR_POS_MINUS+1] = ((pos_minus>>8) & 0xFF)

    with open('eeprom_write.bin', 'wb') as eeprom_file:
        eeprom_file.write(eeprom_content)

    print('Writing new EEPROM...')
    subprocess.run(avrdude_header + ['-U', 'eeprom:w:eeprom_write.bin'])


if __name__ == '__main__':
    main()

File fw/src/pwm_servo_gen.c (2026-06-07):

#include <avr/interrupt.h>
#include "pwm_servo_gen.h"
#include "io.h"

static volatile int16_t _angle;
static volatile int16_t _angle_buf;
static volatile bool _should_generate = false;

// output signal range: 8750-9750 (PWM_ANGLE_MAX) ~ 0.5-2.5 ms pulse (extended sweep)
#define ANGLE_TO_OCR1A 8750

static inline void _pwm_servo_start(uint16_t angle) {
	OCR1A = angle + ANGLE_TO_OCR1A;
	TCCR1B |= (1 << CS11); // Clock source = prescaler 8× ~ 1 MHz
}

static inline void _pwm_servo_stop(void) {
	TCCR1B &= 0xF8; // CS10=0,CS11=0,CS12=0
}

static inline bool _pwm_output_pin_state(void) {
	return (PINB & (1 << PB1)) > 0;
}

void pwm_servo_init(void) {
	// Setup 16-bit timer 1 for hardware PWM generation
	TCCR1A = (1 << COM1A1) | (1 << COM1A0); // OC1A on Compare Match high level
	TCCR1B = (1 << WGM13); // Phase&freq correct PWM TOP=ICR1
	TIMSK |= (1 << OCIE1A) | (1 << OCIE1B);
	ICR1 = 10000; // top value ~ 50 Hz ~ 20 ms period
	OCR1B = 0;
}

void pwm_servo_gen(int16_t angle) {
	if (angle > PWM_ANGLE_MAX)
		return;

	_angle = angle;

	if (!pwm_servo_generating()) {
		// start PWM generation
		TCNT1 = 0;
		_should_generate = true;
		_pwm_servo_start(angle);
	}
}

void pwm_servo_stop(void) {
	_should_generate = false;
	if (!_pwm_output_pin_state())
		_pwm_servo_stop();
}

bool pwm_servo_generating(void) {
	return (TCCR1B & 0x07) > 0; // if any clock source is selected
}

ISR(TIMER1_COMPA_vect) {
	if (!_pwm_output_pin_state()) {
		// On trailing edge → possibly stop PWM
		if (!_should_generate)
			_pwm_servo_stop();
	}
}

ISR(TIMER1_COMPB_vect) {
	// Interrupt after full period → update pwm width
	OCR1A = _angle + ANGLE_TO_OCR1A;
}

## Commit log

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2021-12-02 Add empty schematics & pcb.
    [hwexla.kicad_pcb, hwexla.sch]
2021-12-04 Add hierarchical schematics & add power part.
    [hwexla.sch, io.sch, power.sch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]
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2021-12-04 Add ubschematics to main schematic.
    [hwexla.sch, io.sch, relay.sch]
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2021-12-04 Add servo protection, ass ESD protection.
    [hwexla.sch, io.sch]
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2021-12-04 Add D before IO stabilizer.
    [hwexla.sch, io.sch, power.sch]
2021-12-04 Annotate parts, fix ERC.
    [hwexla.sch, io.sch, power.sch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]
2021-12-04 Power relay from servo power.
    [hwexla.sch, relay.sch]
2021-12-05 Add footprints, use RY8310 stepdown, add footprint library.
    [hwexla.sch, io.sch, power.sch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]
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2021-12-05 Add basic PCB outline.
    [hwexla.kicad_pcb, hwexla.sch, io.sch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]
2021-12-05 Use ATmega328 MCU (it fits).
    [hwexla.kicad_pcb, hwexla.sch]
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2021-12-07 Use transiles as ESD protection.
    [hwexla.kicad_pcb, hwexla.sch, power.sch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]
2021-12-08 Fix switch IN+ & IN-.
    [hwexla.sch]
2021-12-08 Fix switched relay outputs.
    [hwexla.sch]
2021-12-21 Add pcb dimensions & position servo.
    [hwexla.kicad_pcb, hwexla.sch]
2021-12-21 Group footrpints into functional blocks (unwired).
    [hwexla.kicad_pcb]
2021-12-22 Add protective resistors to L-BTN, add C to overvolt. prot.
    [hwexla.kicad_pcb, hwexla.sch, io.sch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]
2021-12-22 Wire part of PCB.
    [hwexla.kicad_pcb, io.sch, power.sch]
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2021-12-23 Everything routed, first attempt.
    [hwexla.kicad_pcb, hwexla.sch]
2021-12-23 Stop solder mask on large-current wires.
    [hwexla.kicad_pcb]
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2021-12-23 Use SMF05 instead of SM05.
    [hwexla.kicad_pcb, hwexla.sch, io.sch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]
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2021-12-23 Sch: add page metainformation.
    [io.sch, power.sch, relay.sch]
2021-12-23 Change logic capacitor to 47uF.
    [power.sch]
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2021-12-28 Add alternate MCUs, add testpoints.
    [hwexla.kicad_pcb, hwexla.sch]
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2021-12-29 Add MOSFET gate protection resistors.
    [hwexla.kicad_pcb, io.sch]
2021-12-30 Debug: use pinsocket instead of pinheader.
    [hwexla.kicad_pcb, hwexla.sch]
2021-12-30 Fix too long net.
    [hwexla.kicad_pcb]
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2022-01-20 Migrate to KiCad 6.
    [hwexla.kicad_pcb, hwexla.kicad_sch, hwexla.sch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]
2022-01-20 Fix errors & warnings reported by DRC.
    [hwexla.kicad_pcb, hwexla.kicad_sch, io.kicad_sch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]
2022-01-20 Describe pinout of programming connector.
    [hwexla.kicad_pcb]
2022-01-20 Tweak Makefile fot KiKit v1.
    [hwexla.kicad_pcb]
2022-01-21 Use net between IO & MCU to make schematics more clear.
    [hwexla.kicad_pcb, hwexla.kicad_sch]
2022-03-08 Use more available resistor grid.
    [hwexla.kicad_sch, io.kicad_sch]
2022-03-08 Allow using of SOT353 TVS.
    [hwexla.kicad_pcb, hwexla.kicad_sch]
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2022-03-08 Add missing OSHW logo.
    [hwexla.kicad_pcb, hwexla.kicad_sch]
2022-03-12 Fix bad BT148 pinout & fix connected wires.
    [hwexla.kicad_pcb, io.kicad_sch, power.kicad_sch]
2022-03-17 Fix bad pins mapping on relay.
    [hwexla.kicad_pcb]
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2022-03-21 Fix target position setting.
    [switch.c]
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2022-03-21 Fix bad servo pinout.
    [hwexla.kicad_pcb, hwexla.kicad_sch]
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2022-03-26 Do not read button connected to active LED.
    Avoid LED flickering.
    [io.c, main.c]
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2022-03-26 Disable servo power on fail.
    [main.c]
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2022-03-29 Show fail message in browser.
    [common.h, main.c]
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2022-03-29 Pcb: power relay from main 5V.
    [hwexla.kicad_pcb, hwexla.kicad_sch]
2022-04-17 Fix relay switching.
2022-05-29 Add capacitor to relay power pin.
    [hwexla.kicad_pcb, hwexla.kicad_sch, io.kicad_sch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]
2022-11-13 Fix sending of FW version.
    [common.h]
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2023-06-13 Fix relay footprint.
    [hwexla.kicad_pcb, relay.kicad_sch]
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2023-06-14 Add possible fuses to relays.
    [hwexla.kicad_pcb, hwexla.kicad_sch, relay.kicad_sch]
2023-06-18 Update libraries, add JLCPCB tooling holes.
    [hwexla.kicad_pcb, hwexla.kicad_sch, io.kicad_sch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]
2023-06-18 Make ERC & DRC pass.
    [hwexla.kicad_pcb, hwexla.kicad_sch]
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2023-10-22 Update to KiCad 7.
    [hwexla.kicad_pcb, hwexla.kicad_sch, io.kicad_sch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]
2023-10-22 Use 2920 package for polyfuse.
    [hwexla.kicad_pcb, hwexla.kicad_sch, power.kicad_sch]
2023-10-22 Move F3 so it is not under connector.
    [hwexla.kicad_pcb, hwexla.kicad_sch]
2023-10-25 Use more proper footprint for SMD button.
    [hwexla.kicad_pcb, hwexla.kicad_sch]
2023-10-26 Use 10k for green LED.
    [hwexla.kicad_pcb, hwexla.kicad_sch]
2023-10-26 Increase tolerance of mag. values 20-30 -> 30-40.
    [common.h, main.c]
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2023-10-28 Decreases fuses values 1A -> 0.5A.
    Servo does not need such a big current and PTC takes some time to switch
    off. It's better to switch off in shorter time.
    [power.kicad_sch]
2023-10-28 Diag: allow to move turnout, fail turnout.
    [common.h, diag.c]
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2023-11-08 Calibrate internal oscillator.
    Set OSCCAL at the startup of MCU.
    OSCCAL cannot be read from signature bytes directly, so we must first
    read it via programmer and store it to EEPROM. MCU then reads value
    from EEPROM at startup and sets read value to OSCCAL.
    [common.h, eeprom.c, main.c]
2023-11-08 Change outputs to inputs on fail.
    To allow external manipulation with pins (e.g. trying to activate relay/
    stepdown by hardconnecting external wire).
    [io.c, io.h, main.c]
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2023-11-09 hw: move text on silkscreen.
    [hwexla.kicad_pcb]
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2023-11-10 Add protection on internal inputs, divide stepdown voltage measuring by 2.
    [hwexla.kicad_pcb, hwexla.kicad_sch, io.kicad_sch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]
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2023-11-17 Set all outputs to '1' on fail.
    [io.c, io.h, main.c]
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2023-11-18 Avoid volatile & inline where not neccessarry.
    [main.c]
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2023-11-18 Store & diag fail_count, last_fail.
    [diag.c, eeprom.c, main.c]
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2023-11-18 When watchdog reset occured, store to warnings.
    [common.h, eeprom.c, main.c]
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2023-11-19 Button resets hWexla when in mFail.
    [common.h, diag.c, main.c]
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2023-12-01 Loosen up servo VCC checks (4.5/4.0 V).
    [io.h]
2023-12-01 Change C15 to 100n.
    [hwexla.kicad_sch]
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2023-12-16 Add empty diagnostic PCB.
    [hwexladiag.kicad_pcb, hwexladiag.kicad_sch]
2023-12-16 Add HC05 symbol & footprint.
    [hwexladiag.kicad_sch]
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2024-02-27 diag: remove blue LED.
    [hwexladiag.kicad_pcb, hwexladiag.kicad_sch]
2024-02-27 diag: pin 31 for red LED.
    [hwexladiag.kicad_pcb, hwexladiag.kicad_sch]
2024-02-27 diag: use input resistor 10R.
    [hwexladiag.kicad_pcb, hwexladiag.kicad_sch]
2024-02-28 Use smaller HC05 footprint.
    Make the PCB smaller by 2.8 mm.
    [hwexladiag.kicad_pcb]
2024-02-29 Add jumper for AT pin external connection.
    [hwexladiag.kicad_pcb, hwexladiag.kicad_sch]
2025-02-28 Add wexlacon empty schematic.
    [wexlacon.kicad_pcb, wexlacon.kicad_sch]
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2025-03-01 Enlarge CAN screwdriver holes.
    [wexlacon.kicad_pcb, wexlacon.kicad_sch]
2025-03-06 Several minor enahncements.
    * Corners: larger diameter (smaller PCB).
    * Mark turnout wire hole on silkscreen.
    * Unify connector names with WexlaCon v3.
    * Use D-SUB25 schematic symbol without holes.
    [wexlacon.kicad_pcb, wexlacon.kicad_sch]
2025-03-08 Adapter drill d=1.8 mm.
    [wexlacon.kicad_pcb, wexlacon.kicad_sch]
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2025-10-27 Do not set both target position outputs in mFail mode.
    In case of one wire failure, fake end position signal could be emitted
    which is unacceptable.
    [common.h, main.c]
2026-05-03 Upgrade to KiCad 9.
    [hwexla.kicad_pcb, hwexla.kicad_sch, io.kicad_sch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]
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2026-05-08 Sch: use JLCPCB tooling holes from MountingHole lib.
    [hwexla.kicad_sch]
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2026-05-26 Fix bad L-SERVO-VCC connection.
    [hwexla.kicad_pcb, hwexla.kicad_sch, io.kicad_sch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]
2026-05-27 Fix DRC issues.
    [hwexla.kicad_pcb, hwexla.kicad_sch]
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2026-06-03 Remove B.Mask stop from power wires.
    Max current is limited by fuse to 0.5 A. 2 mm track width is highly
    oversized for 0.5 A, mask stop is not needed.
    [hwexla.kicad_pcb]
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2026-06-07 Fix underflow in small positions.
    [common.h, switch.c]
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2026-06-27 REL: fix bad wire names.
    [hwexla.kicad_pcb, hwexla.kicad_sch, relay.kicad_sch]
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2026-06-27 Fix switched order of relay contacts.
    [wexlacon.kicad_pcb, wexlacon.kicad_sch]

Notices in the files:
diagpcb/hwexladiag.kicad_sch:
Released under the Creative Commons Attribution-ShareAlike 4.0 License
